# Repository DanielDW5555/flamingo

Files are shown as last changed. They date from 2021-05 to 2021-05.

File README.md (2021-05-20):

# Flamingo


This is the first original project I have completed from start to finish. My inspiration for this project was flamingos, and how they are usually seen balanced upright on one leg. The goal of the project was to create a self balancing robot that could stand upright for a short period of time.

The system works by interfacing the LIS3LV02DLTR accelerometer with the STM32F3 microcontroller to monitor the x and z component of acceleration. The data from the accelerometer is then used by a PID control system implemented on the microcontroller which configures the PWM duty cycle of the brushed DC motors.

The following where the requirements I used to design the robot:
  - The robot must be able to stand up right during operation
  - The robot will be powered by a 9V battery
  - All electronic devices will be implemented on a single PCB
  - The size of the PCB will be equal to or smaller than a credit card
  - No price limit on the BOM (Although my wallet will regret this later...)

The assembled robot fulfills the requirements listed above, but the PID controller requires a lot of tuning to get it to stand upright. Having a larger robot would make tuning the PID control system easier.

The following images depict the blank flamingo PCB and the rev 1 schematic.

Blank PCB


Rev 1 schematic
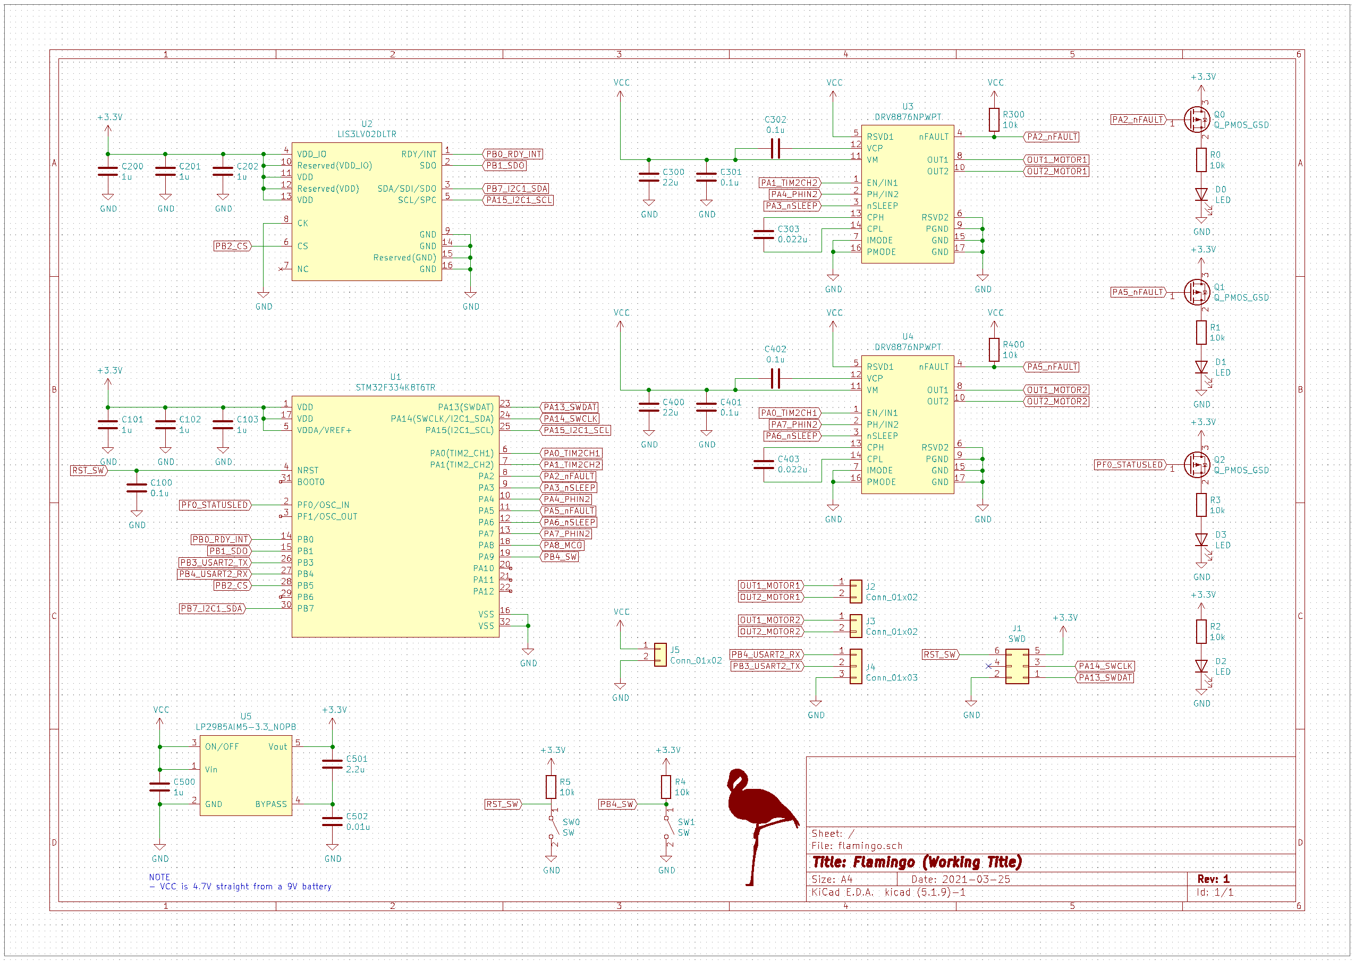
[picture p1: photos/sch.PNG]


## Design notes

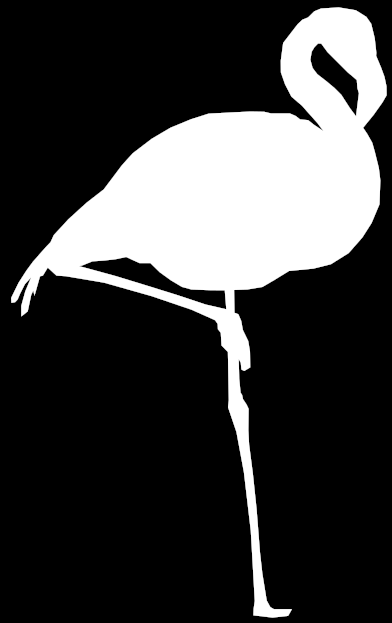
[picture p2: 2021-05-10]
kicad/SWNS_FLAMINGO_LEG_01.bmp

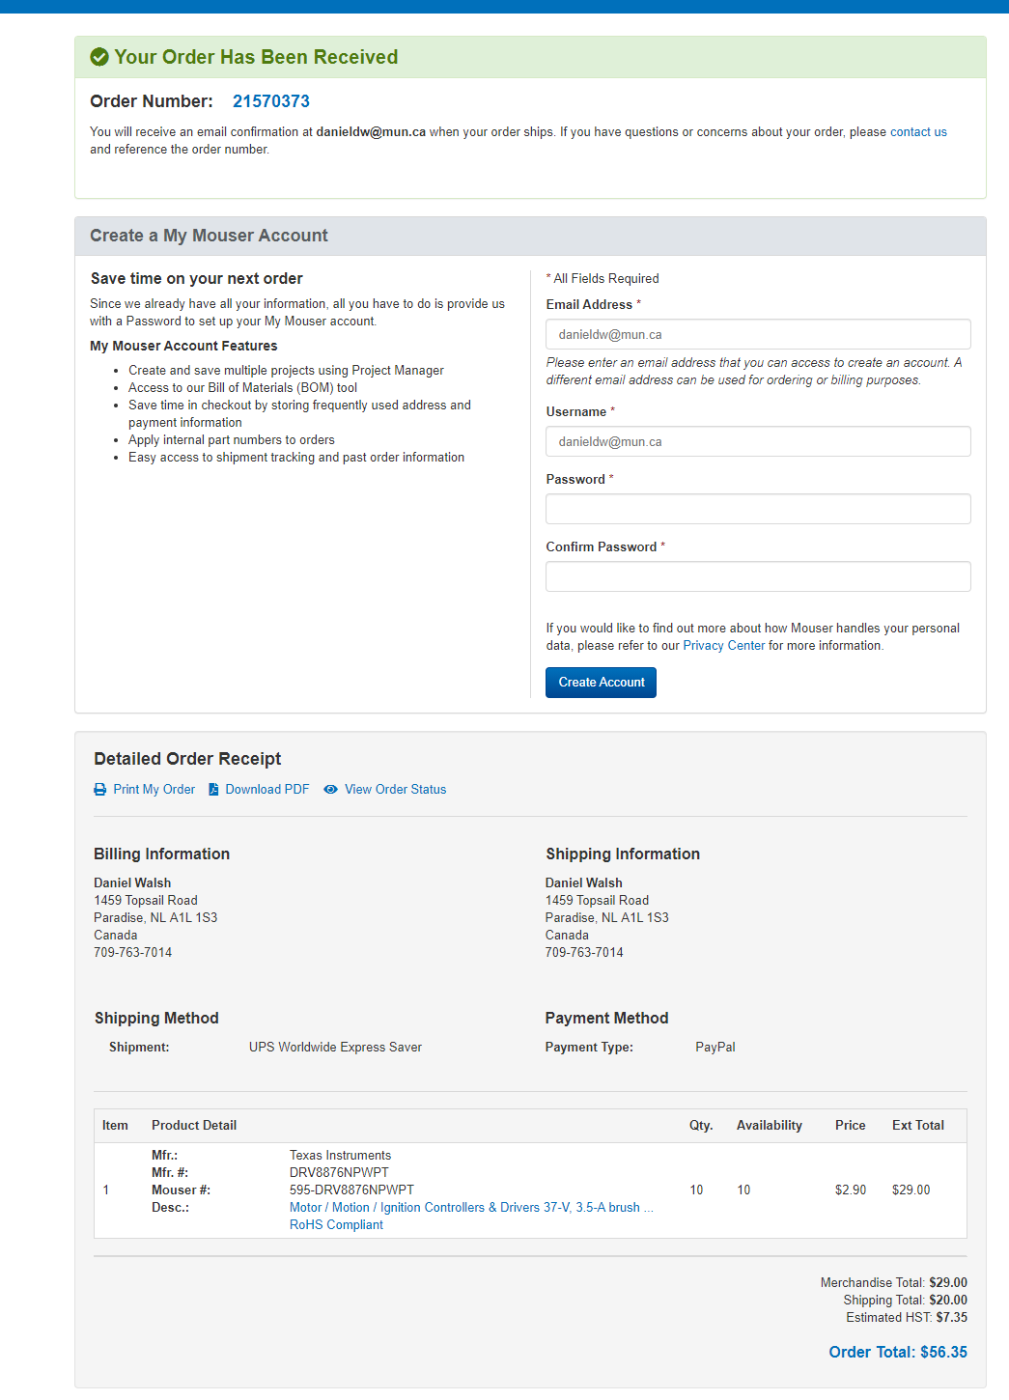
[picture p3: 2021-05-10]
kicad/ohfuckohshit.PNG

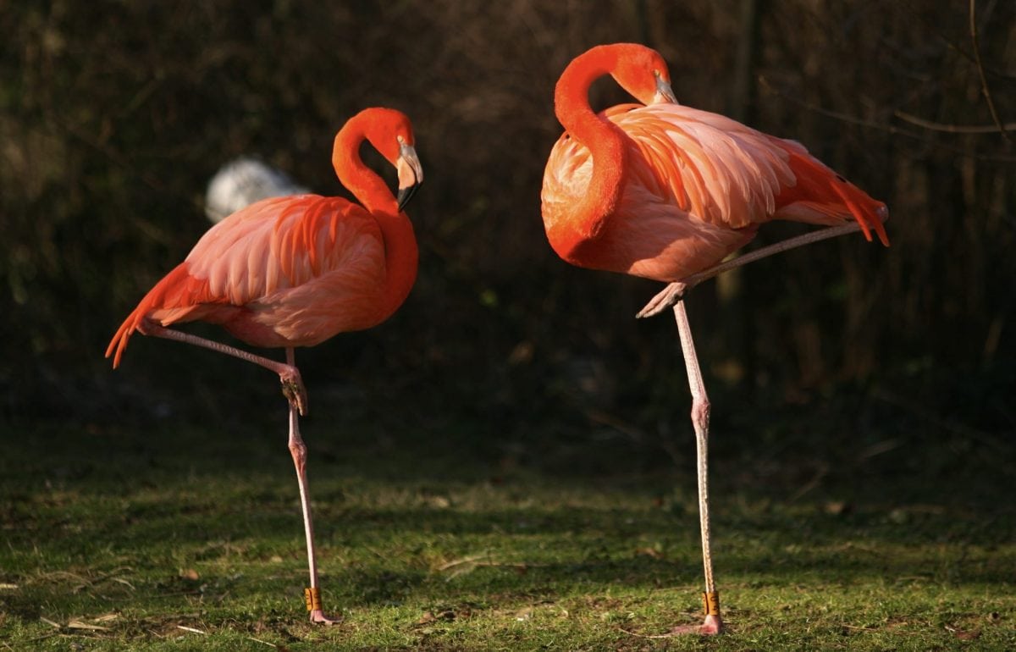
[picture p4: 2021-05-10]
kicad/SWNS_FLAMINGO_LEG_01.jpg

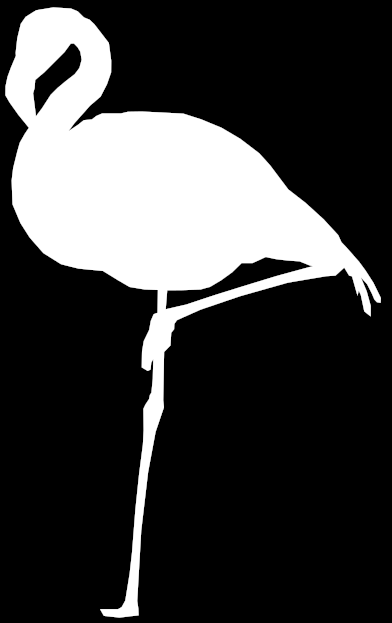
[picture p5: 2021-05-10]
kicad/SWNS_FLAMINGO_LEG_01-L.bmp

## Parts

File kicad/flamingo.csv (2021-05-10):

Reference | Quantity | Value | Footprint | Datasheet | Digikey
C300 C400 | 2 | 22u | Capacitor_SMD:C_1210_3225Metric_Pad1.33x2.70mm_HandSolder | https://content.kemet.com/datasheets/KEM_C1005_Y5V_SMD.pdf | 399-1301-1-ND
C100 C301 C302 C401 C402 | 5 | 0.1u | Capacitor_SMD:C_0603_1608Metric_Pad1.08x0.95mm_HandSolder | https://content.kemet.com/datasheets/KEM_C1090_X7R_ESD.pdf | 399-C0603C104K4REC7867CT-ND
C303 C403 | 2 | 0.022u | Capacitor_SMD:C_0603_1608Metric_Pad1.08x0.95mm_HandSolder | https://content.kemet.com/datasheets/KEM_C1002_X7R_SMD.pdf | C0603C223K3RAC7411
C101 C102 C103 C200 C201 C202 C500 | 7 | 1u | Capacitor_SMD:C_0603_1608Metric_Pad1.08x0.95mm_HandSolder | https://content.kemet.com/datasheets/KEM_C1002_X7R_SMD.pdf | 399-C0603C105K4RAC7411CT-ND
C501 | 1 | 2.2u | Capacitor_SMD:C_0603_1608Metric_Pad1.08x0.95mm_HandSolder | https://content.kemet.com/datasheets/KEM_C1006_X5R_SMD.pdf | 399-7886-1-ND
C502 | 1 | 0.01u | Capacitor_SMD:C_0603_1608Metric_Pad1.08x0.95mm_HandSolder | https://content.kemet.com/datasheets/KEM_C1002_X7R_SMD.pdf | 399-C0603C103M5RAC7411CT-ND
D0 D1 D2 D3 | 4 | LED | LED_SMD:LED_0603_1608Metric_Pad1.05x0.95mm_HandSolder | https://www.kingbrightusa.com/images/catalog/SPEC/APT1608ZGC.pdf | 754-1126-1-ND
J1 | 1 | SWD | Connector_PinSocket_1.27mm:PinSocket_2x03_P1.27mm_Vertical | https://s3.amazonaws.com/catalogspreads-pdf/PAGE94-95%20.050%20MALE%20HDR%20ST%20RA%20SMT.pdf | GRPB032VWVN-RC
J2 J3 | 2 | Conn_01x02 | Connector_PinHeader_2.54mm:PinHeader_1x02_P2.54mm_Vertical_SMD_Pin1Right | https://s3.amazonaws.com/catalogspreads-pdf/PAGE112-113%20.100%20MALE%20HDR.pdf | S1013E-02-ND
J4 | 1 | Conn_01x03 | Connector_PinHeader_2.54mm:PinHeader_1x03_P2.54mm_Vertical_SMD_Pin1Right | https://drawings-pdf.s3.amazonaws.com/11657.pdf | S1013EC-03-ND
J5 | 1 | Conn_01x02 | Connector_PinSocket_2.54mm:PinSocket_2x01_P2.54mm_Vertical_SMD | https://s3.amazonaws.com/catalogspreads-pdf/PAGE112-113%20.100%20MALE%20HDR.pdf | S1013E-02-ND
Q0 Q1 Q2 | 3 | Q_PMOS_GSD | Package_TO_SOT_SMD:SOT-23 | https://www.diodes.com/assets/Datasheets/ds30149.pdf | BSS84-FDICT-ND
R0 R1 R2 R3 R4 R5 R300 R400 | 8 | 10k | Resistor_SMD:R_0603_1608Metric_Pad0.98x0.95mm_HandSolder | https://www.seielect.com/catalog/sei-rmcf_rmcp.pdf | RMCF0603FT10K0CT-ND
SW0 SW1 | 2 | SW | Button_Switch_SMD:SW_SPST_B3U-1000P | https://omronfs.omron.com/en_US/ecb/products/pdf/en-b3u.pdf | SW1020CT-ND
U1 | 1 | STM32F334K8T6TR | Package_QFP:LQFP-32_7x7mm_P0.8mm | https://www.st.com/content/ccc/resource/technical/document/datasheet/d1/cd/3d/18/a2/2c/4e/d0/DM00097745.pdf/files/DM00097745.pdf/jcr:content/translations/en.D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 | 497-STM32F334K8T6TR-ND
U2 | 1 | LIS3LV02DLTR | STMDownloads:LIS3LV02DL | https://www.st.com/content/ccc/resource/technical/document/datasheet/group2/d8/cc/de/55/c6/4d/47/15/CD00091417/files/CD00091417.pdf/jcr:content/translations/e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 | 497-8415-2-ND
U3 U4 | 2 | DRV8876NPWPT | Package_SO:TSSOP-16-1EP_4.4x5mm_P0.65mm | https://www.ti.com/lit/ds/symlink/drv8876n.pdf?ts=1616636876545 | 296-DRV8876NPWPTCT-ND
U5 | 1 | LP2985AIM5-3.3_NOPB | Package_TO_SOT_SMD:SOT-23-5_HandSoldering | https://www.ti.com/lit/ds/symlink/lp2985-n.pdf?HQS=dis-dk-null-digikeymode-dsf-pf-null-wwe&ts=1616878565202 | LP2985AIM5-3.3/NOPBTR-ND

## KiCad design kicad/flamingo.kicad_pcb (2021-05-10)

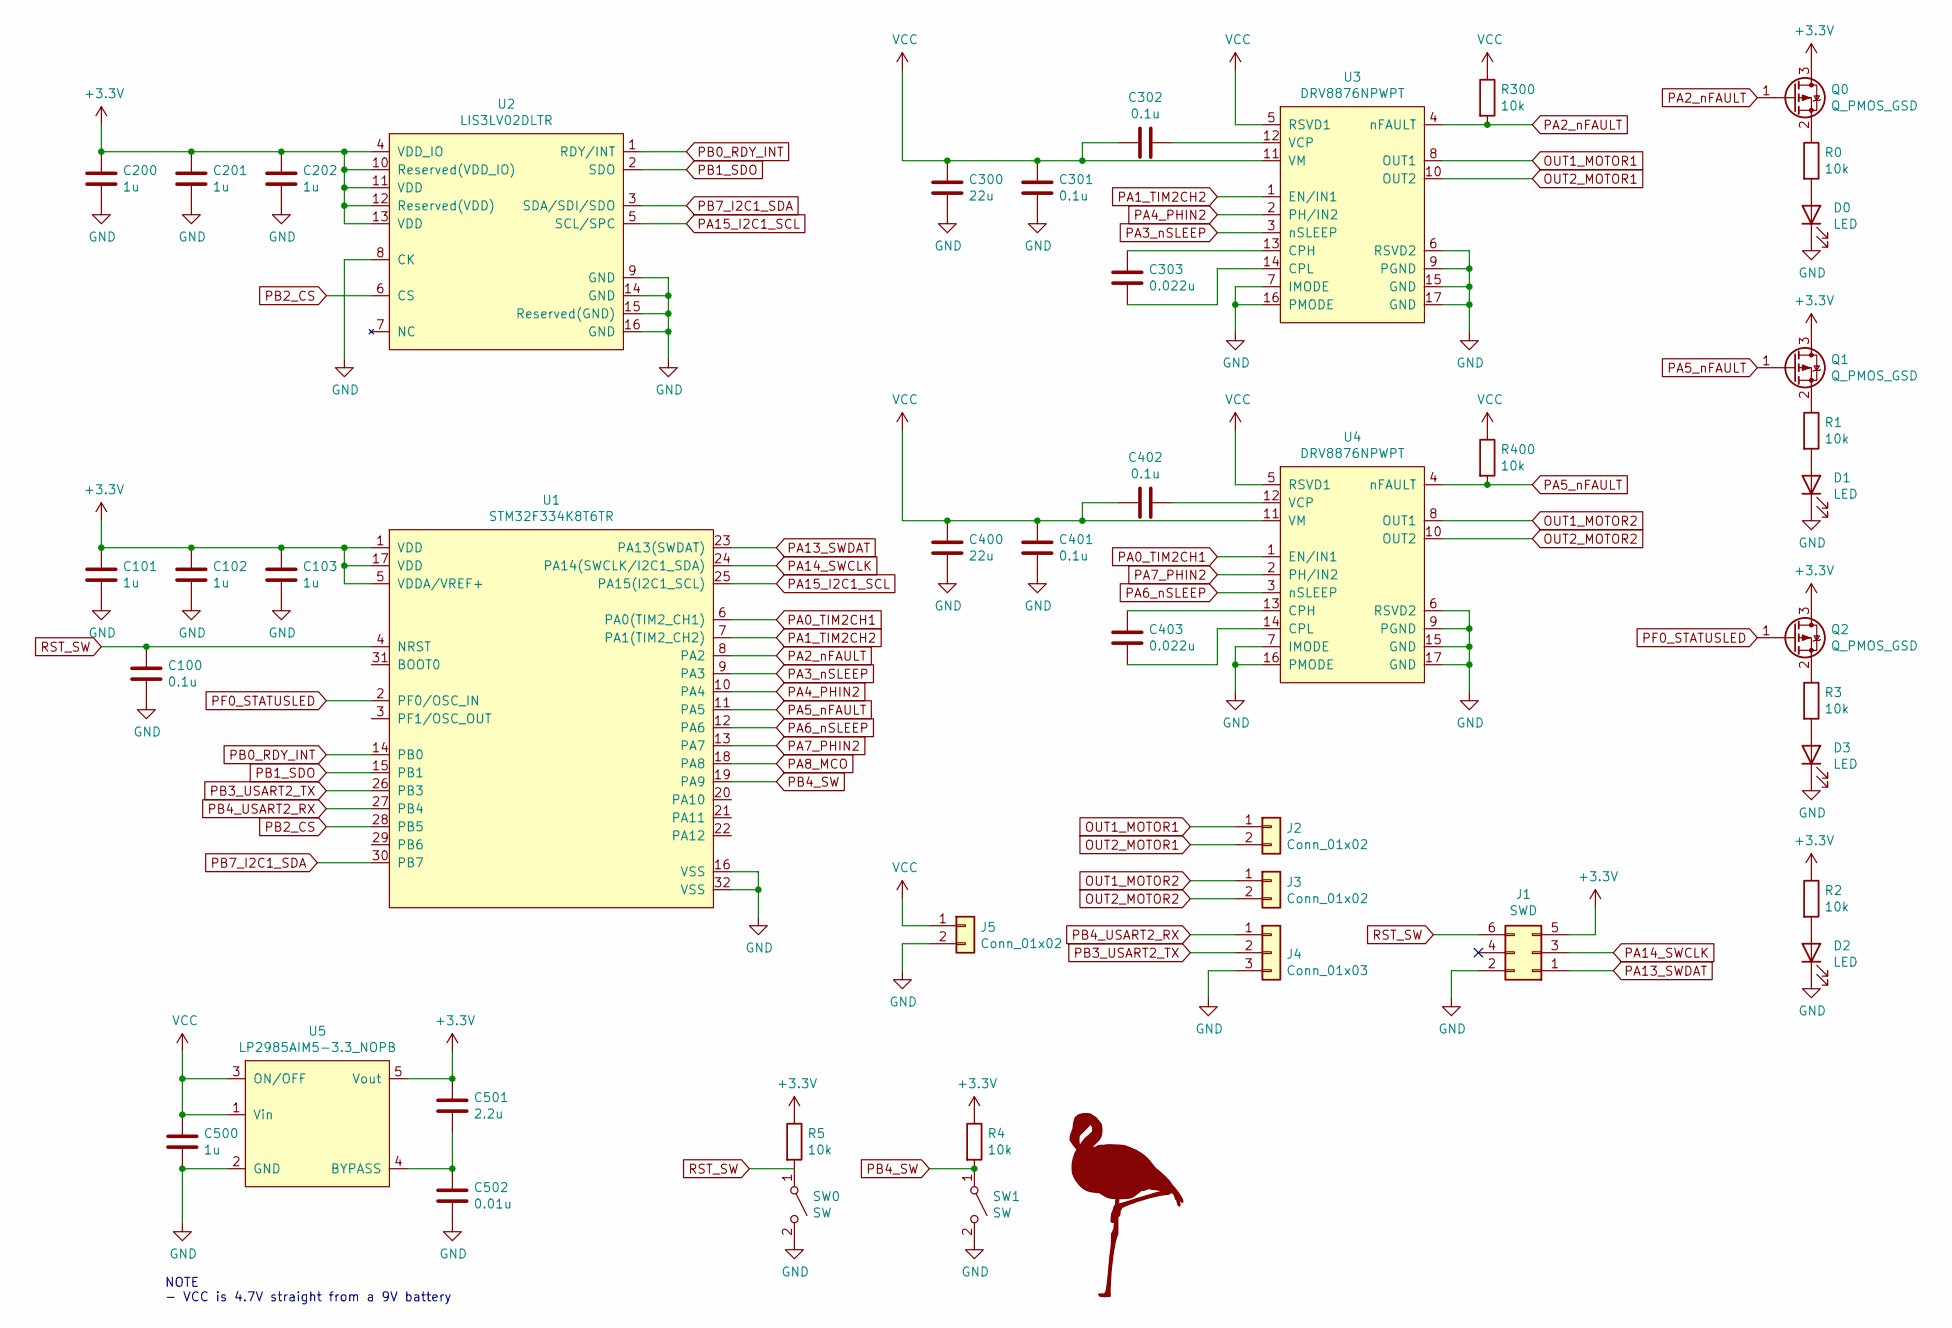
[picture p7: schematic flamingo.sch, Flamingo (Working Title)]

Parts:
C100, C301, C302, C401, C402: 0.1u; C_0603_1608Metric_Pad1.08x0.95mm_HandSolder; Digikey 399-C0603C104K4REC7867CT-ND
C101, C102, C103, C200, C201, C202, C500: 1u; C_0603_1608Metric_Pad1.08x0.95mm_HandSolder; Digikey 399-C0603C105K4RAC7411CT-ND
C300, C400: 22u; C_1210_3225Metric_Pad1.33x2.70mm_HandSolder; Digikey 399-1301-1-ND
C303, C403: 0.022u; C_0603_1608Metric_Pad1.08x0.95mm_HandSolder; Digikey C0603C223K3RAC7411
C501: 2.2u; C_0603_1608Metric_Pad1.08x0.95mm_HandSolder; Digikey 399-7886-1-ND
C502: 0.01u; C_0603_1608Metric_Pad1.08x0.95mm_HandSolder; Digikey 399-C0603C103M5RAC7411CT-ND
D0, D1, D2, D3: LED; LED_0603_1608Metric_Pad1.05x0.95mm_HandSolder; Digikey 754-1126-1-ND
J1: SWD; PinSocket_2x03_P1.27mm_Vertical; Digikey GRPB032VWVN-RC
J2, J3: Conn_01x02; PinHeader_1x02_P2.54mm_Vertical_SMD_Pin1Right; Digikey S1013E-02-ND
J4: Conn_01x03; PinHeader_1x03_P2.54mm_Vertical_SMD_Pin1Right; Digikey S1013EC-03-ND
J5: Conn_01x02; PinSocket_2x01_P2.54mm_Vertical_SMD; Digikey S1013E-02-ND
Q0, Q1, Q2: Q_PMOS_GSD; SOT-23; Digikey BSS84-FDICT-ND
R0, R1, R2, R3, R4, R5, R300, R400: 10k; R_0603_1608Metric_Pad0.98x0.95mm_HandSolder; Digikey RMCF0603FT10K0CT-ND
SW0, SW1: SW; SW_SPST_B3U-1000P; Digikey SW1020CT-ND
U1: STM32F334K8T6TR; LQFP-32_7x7mm_P0.8mm; Digikey 497-STM32F334K8T6TR-ND
U2: LIS3LV02DLTR; LIS3LV02DL; Digikey 497-8415-2-ND
U3, U4: DRV8876NPWPT; TSSOP-16-1EP_4.4x5mm_P0.65mm; Digikey 296-DRV8876NPWPTCT-ND
U5: LP2985AIM5-3.3_NOPB; SOT-23-5_HandSoldering; Digikey LP2985AIM5-3.3/NOPBTR-ND

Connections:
+3V3: C101.1, C102.1, C103.1, C200.1, C201.1, C202.1, C501.1, J1.5, Q0.3 (D), Q1.3 (D), Q2.3 (D), R2.1, R4.1, R5.1, U1.1 (VDD), U1.5 (VDDA/VREF+), U1.17 (VDD), U2.4 (VDD_IO), U2.10 (Reserved(VDD_IO)), U2.11 (VDD), U2.12 (Reserved(VDD)), U2.13 (VDD), U5.5 (Vout)
GND: C100.2, C101.2, C102.2, C103.2, C200.2, C201.2, C202.2, C300.2, C301.2, C400.2, C401.2, C500.2, C502.2, D0.1 (K), D1.1 (K), D2.1 (K), D3.1 (K), J1.2, J4.3, J5.2, SW0.2 (B), SW1.2 (B), U1.16 (VSS), U1.32 (VSS), U2.8 (CK), U2.9 (GND), U2.14 (GND), U2.15 (Reserved(GND)), U2.16 (GND), U3.6 (RSVD2), U3.7 (IMODE), U3.9 (PGND), U3.15 (GND), U3.16 (PMODE), U3.17 (GND), U4.6 (RSVD2), U4.7 (IMODE), U4.9 (PGND), U4.15 (GND), U4.16 (PMODE), U4.17 (GND), U5.2 (GND)
unnamed: C302.1, U3.12 (VCP)
unnamed: C303.1, U3.14 (CPL)
unnamed: C303.2, U3.13 (CPH)
unnamed: C402.2, U4.12 (VCP)
unnamed: C403.1, U4.14 (CPL)
unnamed: C403.2, U4.13 (CPH)
unnamed: C501.2, C502.1, U5.4 (BYPASS)
unnamed: D0.2 (A), R0.2
unnamed: D1.2 (A), R1.2
unnamed: D2.2 (A), R2.2
unnamed: D3.2 (A), R3.2
unnamed: Q0.2 (S), R0.1
unnamed: Q1.2 (S), R1.1
unnamed: Q2.2 (S), R3.1
OUT1_MOTOR1: J2.1, U3.8 (OUT1)
OUT1_MOTOR2: J3.1, U4.8 (OUT1)
OUT2_MOTOR1: J2.2, U3.10 (OUT2)
OUT2_MOTOR2: J3.2, U4.10 (OUT2)
PA0_TIM2CH1: U1.6 (PA0(TIM2_CH1)), U4.1 (EN/IN1)
PA1_TIM2CH2: U1.7 (PA1(TIM2_CH2)), U3.1 (EN/IN1)
PA2_nFAULT: Q0.1 (G), R300.2, U1.8 (PA2), U3.4 (nFAULT)
PA3_nSLEEP: U1.9 (PA3), U3.3 (nSLEEP)
PA4_PHIN2: U1.10 (PA4), U3.2 (PH/IN2)
PA5_nFAULT: Q1.1 (G), R400.2, U1.11 (PA5), U4.4 (nFAULT)
PA6_nSLEEP: U1.12 (PA6), U4.3 (nSLEEP)
PA7_PHIN2: U1.13 (PA7), U4.2 (PH/IN2)
PA8_MCO: U1.18 (PA8)
PA13_SWDAT: J1.1, U1.23 (PA13(SWDAT))
PA14_SWCLK: J1.3, U1.24 (PA14(SWCLK/I2C1_SDA))
PA15_I2C1_SCL: U1.25 (PA15(I2C1_SCL)), U2.5 (SCL/SPC)
PB0_RDY_INT: U1.14 (PB0), U2.1 (RDY/INT)
PB1_SDO: U1.15 (PB1), U2.2 (SDO)
PB2_CS: U1.28 (PB5), U2.6 (CS)
PB3_USART2_TX: J4.2, U1.26 (PB3)
PB4_SW: R4.2, SW1.1 (A), U1.19 (PA9)
PB4_USART2_RX: J4.1, U1.27 (PB4)
PB7_I2C1_SDA: U1.30 (PB7), U2.3 (SDA/SDI/SDO)
PF0_STATUSLED: Q2.1 (G), U1.2 (PF0/OSC_IN)
RST_SW: C100.1, J1.6, R5.2, SW0.1 (A), U1.4 (NRST)
VCC: C300.1, C301.1, C302.2, C400.1, C401.1, C402.1, C500.1, J5.1, R300.1, R400.1, U3.5 (RSVD1), U3.11 (VM), U4.5 (RSVD1), U4.11 (VM), U5.1 (Vin), U5.3 (ON/OFF)

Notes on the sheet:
NOTE - VCC is 4.7V straight from a 9V battery

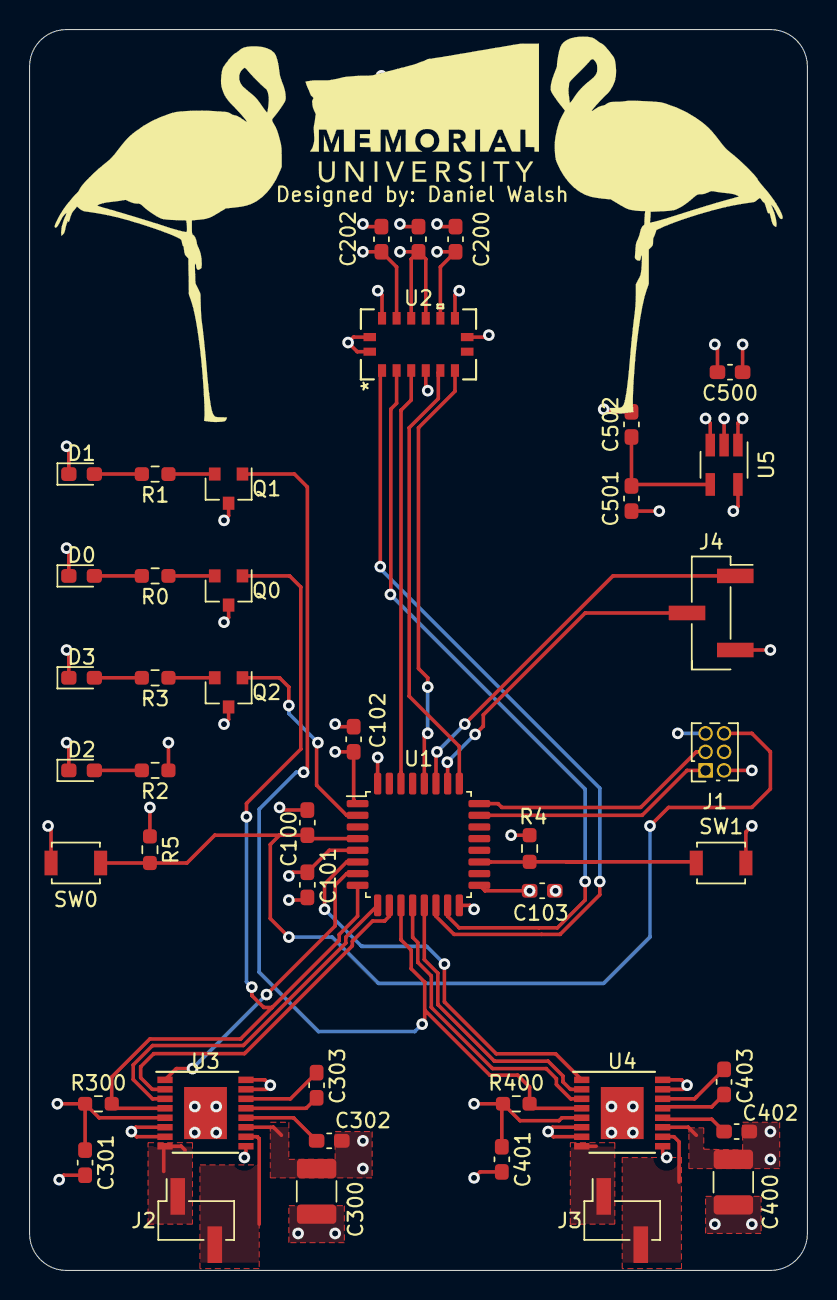
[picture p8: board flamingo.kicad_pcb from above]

Board: 4 copper layers, 53.3 x 85.1 mm, 45 parts (1 on the bottom side), 41 nets.

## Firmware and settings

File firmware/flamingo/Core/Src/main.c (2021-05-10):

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
/* Includes ------------------------------------------------------------------*/
#include "main.h"

/* USER CODE BEGIN Includes */
#include <string.h>
#include <stdio.h>

/* USER CODE END Includes */

I2C_HandleTypeDef hi2c1;

TIM_HandleTypeDef htim2;

UART_HandleTypeDef huart2;

/* USER CODE BEGIN PV */
UART_HandleTypeDef huart2;
uint8_t uartTest[5] = "Peep!";

I2C_HandleTypeDef hi2c1;
// Register values
uint8_t LD_ADDR = 0b00011101 << 1;
const uint8_t reg_whoAmI = 0x0F;
const uint8_t reg_offset_x = 0x16;
const uint8_t reg_offset_y = 0x17;
const uint8_t reg_offset_z = 0x18;
const uint8_t reg_ctrl_reg1 = 0x20;
const uint8_t reg_ctrl_reg2 = 0x21;
const uint8_t reg_ctrl_reg3 = 0x22;
const uint8_t reg_outX_l = 0x28;
const uint8_t reg_outX_h = 0x29;
const uint8_t reg_outY_l = 0x2A;
const uint8_t reg_outY_h = 0x2B;
const uint8_t reg_outZ_l = 0x2C;
const uint8_t reg_outZ_h = 0x2D;

const uint16_t x_offset = 500;
const uint16_t z_offset = 280;

//const uint16_t pid_target = 1024;
const uint16_t pid_target = 1050;
const uint16_t pid_target_range = 100;
int16_t pid_error;
float pid_kp = 0.92;
float pid_ki = 0.0000;
float pid_kd = 0.39;
float pid_proportional = 0;
float pid_integral = 0;
float pid_derivative = 0;
float pid_combinedError = 0;
float pid_lastError = 0;
float pid_totalError = 0;
float pid_dc_offset = 15;

uint16_t motarDuty = 0;


/* USER CODE END PV */

void SystemClock_Config(void);
static void MX_GPIO_Init(void);
static void MX_USART2_UART_Init(void);
static void MX_I2C1_Init(void);
static void MX_TIM2_Init(void);
/* USER CODE BEGIN PFP */
void isDeviceAlive(uint8_t);
void initLDDevice(void);
void initMotors();
void i2cWriteOneByte(uint8_t, uint8_t, uint8_t);
void setMotorDirectionForwards();
void setMotorDirectionBackwards();
uint8_t i2cReadOneByte(uint8_t, uint8_t);
uint16_t getJustifiedData(uint8_t, uint8_t);
uint16_t twosComplement(uint16_t);
uint8_t checkDirection(uint16_t);
/* USER CODE END PFP */

/**
  * @brief  The application entry point.
  * @retval int
  */
int main(void)
{
  /* USER CODE BEGIN 1 */
  uint8_t buf[12];

  /* USER CODE END 1 */

  /* MCU Configuration--------------------------------------------------------*/

  /* Reset of all peripherals, Initializes the Flash interface and the Systick. */
  HAL_Init();

  /* Configure the system clock */
  SystemClock_Config();

  /* Initialize all configured peripherals */
  MX_GPIO_Init();
  MX_USART2_UART_Init();
  MX_I2C1_Init();
  MX_TIM2_Init();
  /* USER CODE BEGIN 2 */

  // Start of program
  // Configure device so its ready to print data
  initLDDevice();

  // Check if i2c device(s) are alive
  isDeviceAlive(LD_ADDR);

  // Initialises motars
  initMotors();

  // Tests each motor for their speed and direction
  // testMotors();

  /* USER CODE END 2 */

  /* Infinite loop */
  /* USER CODE BEGIN WHILE */
  while (1)
  {
	  // Blink LED
	  HAL_GPIO_TogglePin(GPIOF, GPIO_PIN_0);

	  // Gets acceleration data from LD device
	  uint16_t outX = getJustifiedData(reg_outX_l, reg_outX_h);
	  float gX = twosComplement(outX) - x_offset;

	  uint16_t outZ = getJustifiedData(reg_outZ_l, reg_outZ_h) + z_offset;
	  uint8_t direction = checkDirection(outZ);
	  float gZ = outZ;



	  // --- PID Control code ---
	  // Calculate the error between the desired target
	  pid_error = (pid_target - gX)/1;

	  if(pid_target-pid_target_range < pid_target < pid_target+pid_target_range)
	  {
		  // Set direction of motors to be correct
		  	  if(direction == 1)
		  	  {
		  		  setMotorDirectionForwards();
		  	  }
		  	  else
		  	  {
		  		  setMotorDirectionBackwards();
		  	  }

	  // Calculate the integral error
	  if(pid_error != 0)
	  {
		  pid_totalError += pid_error;
	  }
	  else
	  {
		  pid_totalError = 0;
	  }

	  // Calculate all errors in PID controller
	  pid_proportional = pid_error * pid_kp;
	  pid_integral = pid_totalError * pid_ki;
	  pid_derivative = (pid_error - pid_lastError) * pid_kd;

	  pid_lastError = pid_error;

	  pid_combinedError = pid_proportional + pid_integral + pid_derivative;



	  // Flips sign if total error is negative
	  if(pid_combinedError < 0)
	  {
		  pid_combinedError *= -1;
	  }
	  if(pid_combinedError >= 256)
	  {
		  pid_combinedError = 256;
	  }

	  // Due to accelerometer calibration errors, a DC bias is added to the control loop when flamingo is tilted forwards
	  if(direction == 1)
	  {
		pid_combinedError += pid_dc_offset;
	  }

	  // Set the motor drivers duty
	  motarDuty = pid_combinedError;
	  TIM2->CCR1 = motarDuty+pid_dc_offset;
	  TIM2->CCR2 = motarDuty+pid_dc_offset;

	  }
	  else
	  {
		  TIM2->CCR1 = 0;
		  TIM2->CCR2 = 0;
	  }

	  // --- End of PID Control code ---

    /* USER CODE END WHILE */

    /* USER CODE BEGIN 3 */
  }
  /* USER CODE END 3 */
}

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
/* USER CODE BEGIN 4 */
// User Functions

// Blinks LED quickly 3 times
void ledSuccess()
{
	for(int i = 0; i < 6; i ++)
	{
		HAL_GPIO_TogglePin(GPIOF, GPIO_PIN_0);
		HAL_Delay(50);
	}
}

// Checks if device is alive, if so it blinks LED fast 5 times
void isDeviceAlive(uint8_t slaveAddress)
{
	if(HAL_I2C_IsDeviceReady(&hi2c1, LD_ADDR, 5, 100) == HAL_OK)
	{
		ledSuccess();
	}
}

// Writes one byte to the a register
void i2cWriteOneByte(uint8_t slaveAddress, uint8_t regAddress, uint8_t data)
{
	uint8_t buf[2];

	buf[0] = 0x20;
	buf[1] = 0xCF;
  	HAL_I2C_Master_Transmit(&hi2c1, LD_ADDR, buf, 2, 100);
}

// Reads one byte on slave device
uint8_t i2cReadOneByte(uint8_t slaveAddress, uint8_t regAddress)
{
	uint8_t buf[1];
	uint8_t buf2[1];
	buf[0] = regAddress;
	HAL_I2C_Master_Transmit(&hi2c1, slaveAddress, buf, 1, 100);

	HAL_I2C_Master_Receive(&hi2c1, LD_ADDR, buf2, 1, 100);
	return buf2[0];
}

// Combines low and high bytes to get the justified data
uint16_t getJustifiedData(uint8_t LSBAddress, uint8_t HSBAddress)
{
	int16_t justifiedData;
	uint8_t lsbData = i2cReadOneByte(LD_ADDR, LSBAddress);
	uint8_t hsbData = i2cReadOneByte(LD_ADDR, HSBAddress);

	justifiedData = ((lsbData | ((int16_t)hsbData << 8 )) & 0x0FFF);

	// Compute twos complement
	if(justifiedData > 0x7FF)
	{
		justifiedData |= 0xF000;
		// Gets magnitude for twos complement
		// justifiedData = ((~justifiedData) + 1) & 0x0FFF;
	}

	return(justifiedData);
}

// Returns the twos complement of a 12 bit number
uint16_t twosComplement(uint16_t data)
{
	//if(data > 0x07FF)
	if(data > 0x07FF)
	{
		data = (((~data) + 1) & 0x0FFF);
	}
	return(data);
}

// Checks the direction of which way the board is tilting
// If it returns 0, it if tilting backwards
// If it returns 1, it is tilting forwards
uint8_t checkDirection(uint16_t data)
{
	uint8_t direction = 0;

	if(data > 0x07FF)
	{
		direction = 1;
	}

	return(direction);
}

// Inits LD device
void initLDDevice(void)
{
	// Set CS high
	HAL_GPIO_WritePin(GPIOB, GPIO_PIN_5, 1);
	// Turn on device for measurements
	i2cWriteOneByte(LD_ADDR, 0x20, 0xCF);

	// Reads the who am I register and outputs it on UART
	uint8_t data = i2cReadOneByte(LD_ADDR, reg_whoAmI);
	HAL_UART_Transmit(&huart2, &data, 1, 100);
}

// Start PWM channels on DRV devices
void initMotors()
{
	// Turn on PWM
	HAL_TIM_PWM_Start(&htim2, TIM_CHANNEL_1);
	HAL_TIM_PWM_Start(&htim2, TIM_CHANNEL_2);

	// Enable devices
	HAL_GPIO_WritePin(GPIOA, GPIO_PIN_3, 1);
	HAL_GPIO_WritePin(GPIOA, GPIO_PIN_6, 1);
}

// Tests motars on their speed and direction
// Note:	Forward direction: pin4=1, pin7=0
//			Backward direction: pin4=0, pin7=1
void testMotors()
{
	HAL_GPIO_TogglePin(GPIOA, GPIO_PIN_7);

	for(int j = 0; j < 2; j ++)
	{
		for(int i = 0; i < 256; i ++)
		{
			if(i > 00)
				TIM2->CCR1 = i+00;
				TIM2->CCR2 = i+00;
			HAL_Delay(10);
		}
		for(int i = 256; i > 5; i --)
		{
			TIM2->CCR1 = i+00;
			TIM2->CCR2 = i+00;
			HAL_Delay(10);
		}
		HAL_GPIO_TogglePin(GPIOA, GPIO_PIN_4);
		HAL_GPIO_TogglePin(GPIOA, GPIO_PIN_7);
	}
}

// Sets the motor direction forwards
void setMotorDirectionForwards()
{
	HAL_GPIO_WritePin(GPIOA, GPIO_PIN_4, 1);
	HAL_GPIO_WritePin(GPIOA, GPIO_PIN_7, 0);
}

// Sets the motor direction backwards
void setMotorDirectionBackwards()
{
	HAL_GPIO_WritePin(GPIOA, GPIO_PIN_4, 0);
	HAL_GPIO_WritePin(GPIOA, GPIO_PIN_7, 1);
}

/* USER CODE END 4 */
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


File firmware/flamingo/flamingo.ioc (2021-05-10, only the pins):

Mcu.UserName=STM32F334K8Tx
PA13.Signal=SYS_JTMS-SWDIO
PA1.Signal=S_TIM2_CH2
PB7.Signal=I2C1_SDA
PA0.Signal=S_TIM2_CH1_ETR
PB3.Signal=USART2_TX
PA4.Signal=GPIO_Output
PB5.Signal=GPIO_Output
PA6.Signal=GPIO_Output
PA14.Signal=SYS_JTCK-SWCLK
PA15.Signal=I2C1_SCL
PB0.Signal=GPIO_Input
PB4.Signal=USART2_RX
PA3.Signal=GPIO_Output
PA7.Signal=GPIO_Output

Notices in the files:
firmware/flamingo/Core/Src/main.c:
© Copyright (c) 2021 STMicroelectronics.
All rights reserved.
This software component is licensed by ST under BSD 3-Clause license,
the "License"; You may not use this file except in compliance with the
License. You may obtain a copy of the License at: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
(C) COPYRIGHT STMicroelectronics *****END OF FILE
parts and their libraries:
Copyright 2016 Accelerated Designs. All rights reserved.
